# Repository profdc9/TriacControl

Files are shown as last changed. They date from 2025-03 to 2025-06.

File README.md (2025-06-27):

# TriacControl

This is an optoisolated triac motor speed controller where the phase control of the motor AC signal may be controlled by an analog or PWM signal.
Typically, a universal motor tool such as a drill or a router could have it's speed varied this way.
A PWM signal would usually be supplied by a microcontroller.  This motor speed control is open-loop and you have to add a tachometer
if you want to be able to vary the motor speed to achieve a particular rotation rate.

The voltage for the control may be 3.3 v, 5v, or up to 24 v.  A resistor (one of R17,R18,R19) and a capacitor (one of C2,C3,C4) determine how
the voltage/PWM signal varies the motor speed control.  The minimum control voltage to turn on the triac is about 1.75 V.  3.3V control uses
a 100 ohm resistor and a 22 uF capacitor, a 5 V control uses a 470 ohm resistor and a 47 uF capacitor, 12 volts uses a 2k2 resistor and 47 uF
capacitor, and 24 V uses a 4k7 resistor an 47 uF capacitor.  You may have to experiment to get it to put the control voltage into the required
range.  If you have an incandescent light bulb, you can use that as the load rather than the motor to see how bright it gets as you vary the
control voltage.  Three resistors and three capacitors may be placed on the board and selected using jumpers so that soldering need not be performed
to try different values.

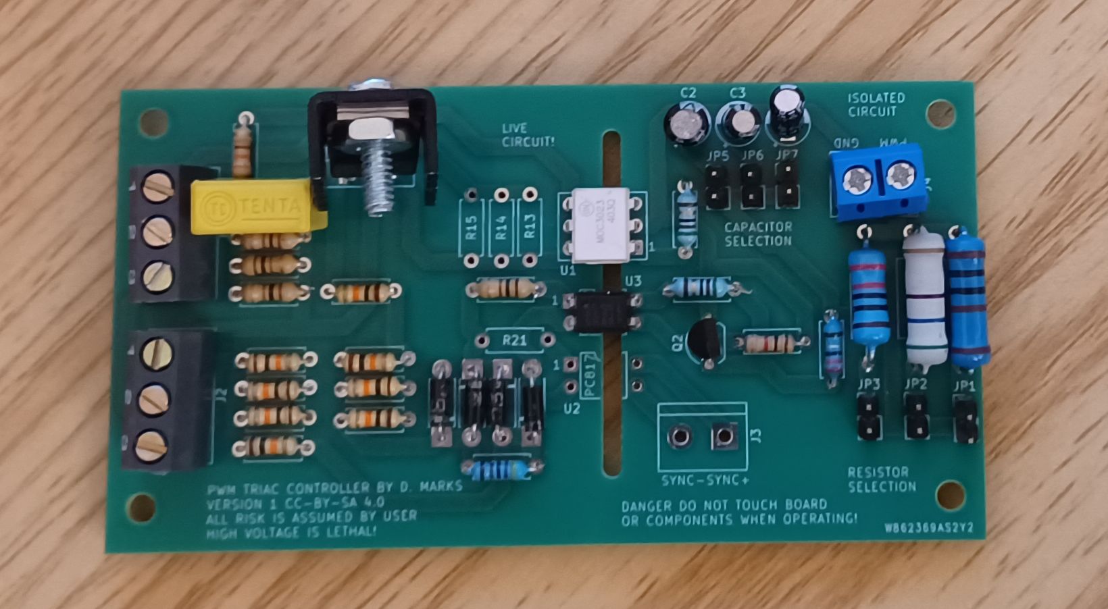
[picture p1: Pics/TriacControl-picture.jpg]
TriacControl


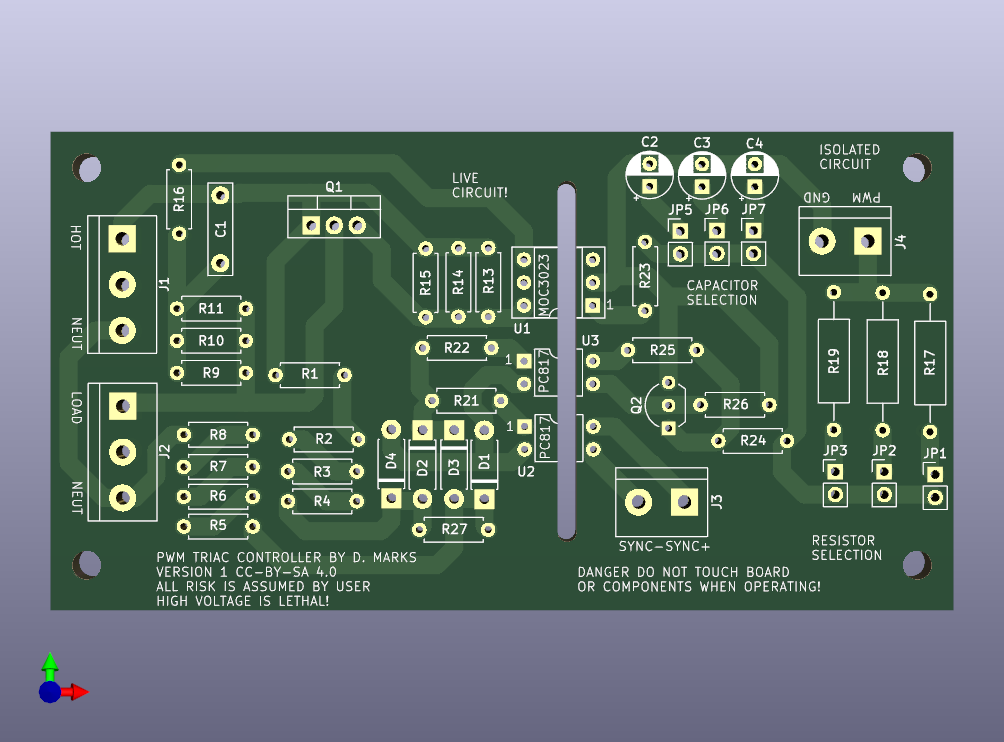
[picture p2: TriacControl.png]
TriacControl


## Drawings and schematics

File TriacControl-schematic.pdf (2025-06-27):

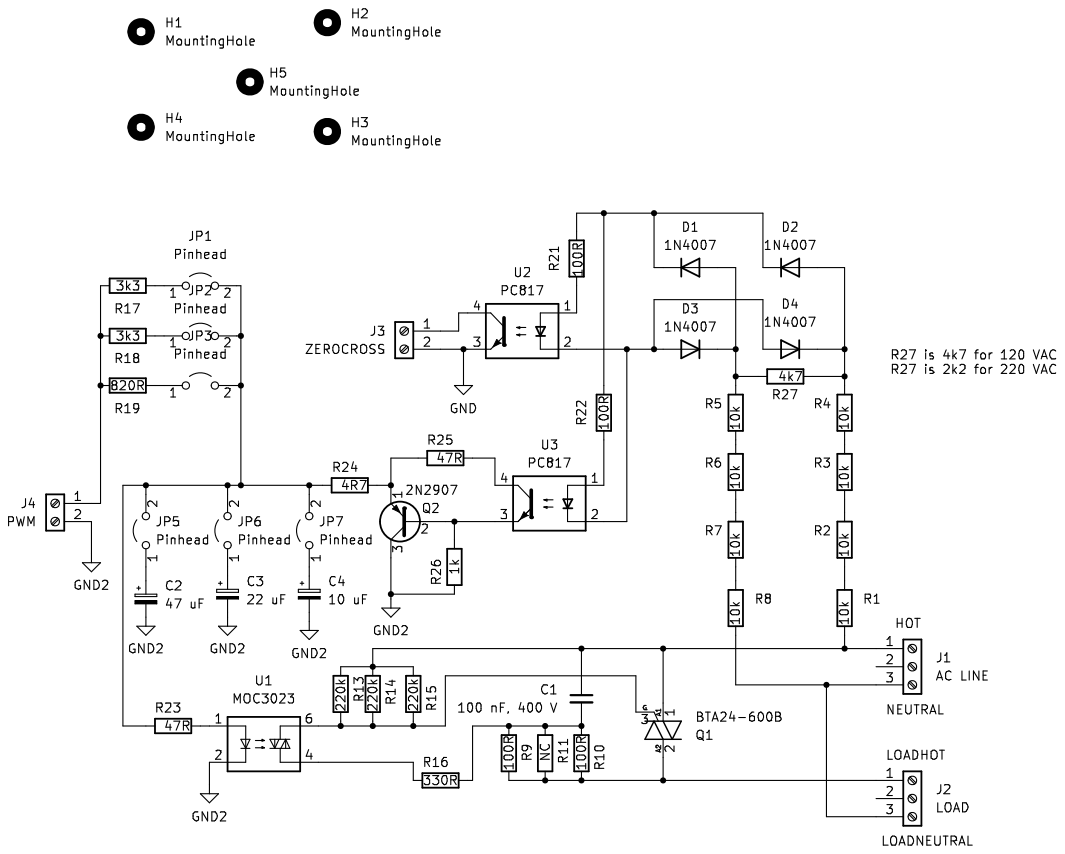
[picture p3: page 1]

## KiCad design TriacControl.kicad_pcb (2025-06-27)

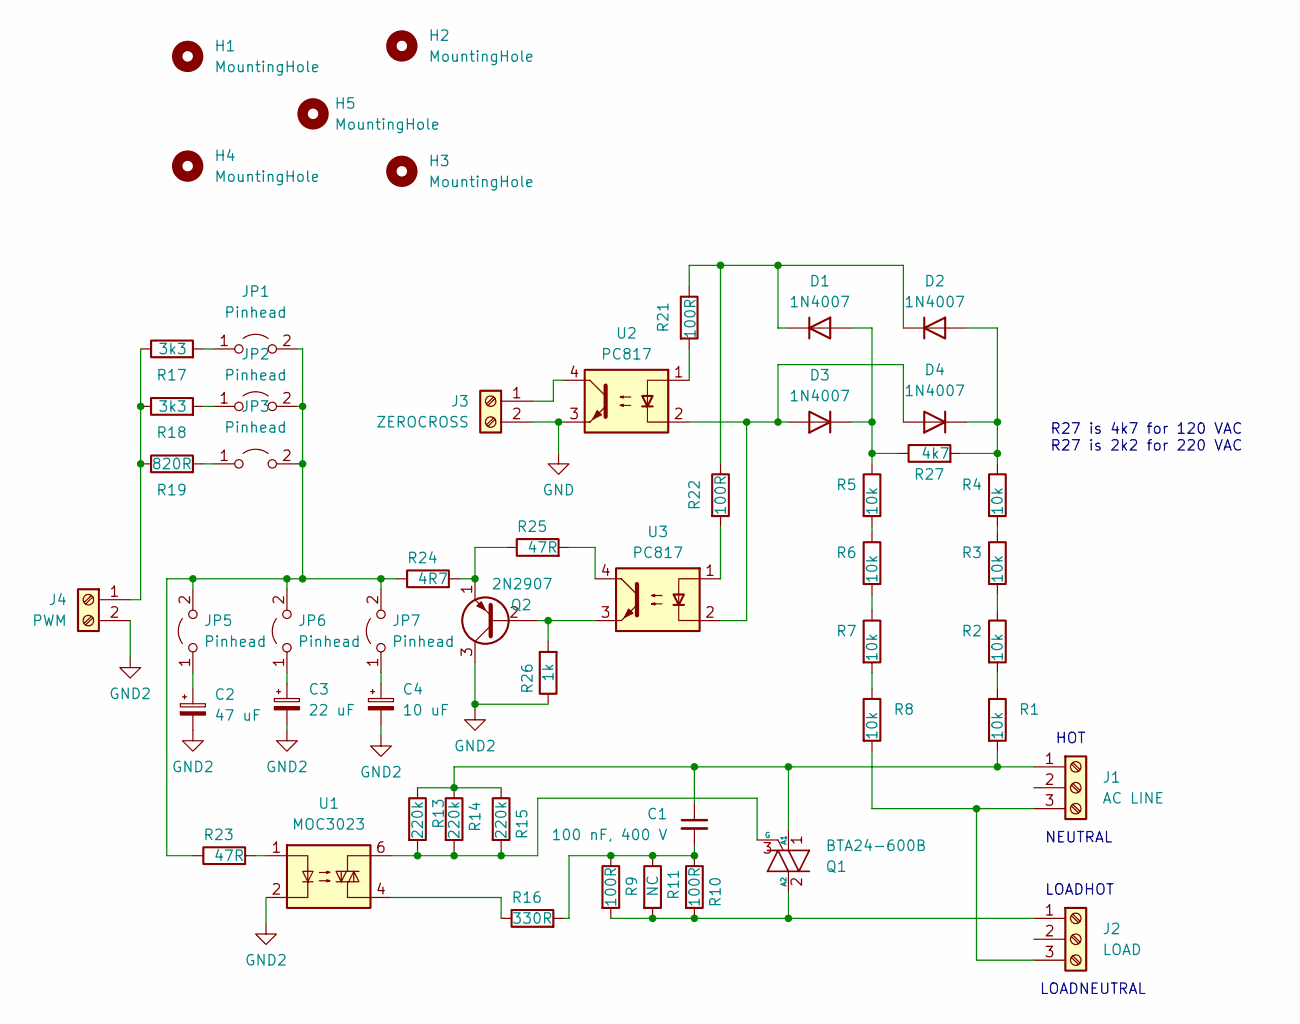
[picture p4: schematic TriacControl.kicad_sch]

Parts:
C1: 100 nF, 400 V; C_Rect_L10.0mm_W2.5mm_P7.50mm_MKS4
C2: 47 uF; CP_Radial_D5.0mm_P2.50mm
C3: 22 uF; CP_Radial_D5.0mm_P2.50mm
C4: 10 uF; CP_Radial_D5.0mm_P2.50mm
D1, D2, D3, D4: 1N4007; D_DO-41_SOD81_P7.62mm_Horizontal
H1, H2, H3, H4: MountingHole; MountingHole_3.2mm_M3
H5: MountingHole; MountingHole_2.1mm
J1: AC LINE; TerminalBlock_bornier-3_P5.08mm
J2: LOAD; TerminalBlock_bornier-3_P5.08mm
J3: ZEROCROSS; TerminalBlock_bornier-2_P5.08mm
J4: PWM; TerminalBlock_bornier-2_P5.08mm
JP1, JP2, JP3, JP5, JP6, JP7: Pinhead; PinHeader_1x02_P2.54mm_Vertical
Q1: BTA24-600B; TO-220-3_Vertical
Q2: 2N2907; TO-92_Inline_Wide
R1, R2, R3, R4, R5, R6, R7, R8: 10k; R_Axial_DIN0207_L6.3mm_D2.5mm_P7.62mm_Horizontal
R9, R10, R21, R22: 100R; R_Axial_DIN0207_L6.3mm_D2.5mm_P7.62mm_Horizontal
R11: NC; R_Axial_DIN0207_L6.3mm_D2.5mm_P7.62mm_Horizontal
R13, R14, R15: 220k; R_Axial_DIN0207_L6.3mm_D2.5mm_P7.62mm_Horizontal
R16: 330R; R_Axial_DIN0207_L6.3mm_D2.5mm_P7.62mm_Horizontal
R17, R18: 3k3; R_Axial_DIN0309_L9.0mm_D3.2mm_P15.24mm_Horizontal
R19: 820R; R_Axial_DIN0309_L9.0mm_D3.2mm_P15.24mm_Horizontal
R23, R25: 47R; R_Axial_DIN0207_L6.3mm_D2.5mm_P7.62mm_Horizontal
R24: 4R7; R_Axial_DIN0207_L6.3mm_D2.5mm_P7.62mm_Horizontal
R26: 1k; R_Axial_DIN0207_L6.3mm_D2.5mm_P7.62mm_Horizontal
R27: 4k7; R_Axial_DIN0207_L6.3mm_D2.5mm_P7.62mm_Horizontal
U1: MOC3023; DIP-6_W7.62mm_Socket
U2, U3: PC817; DIP-4_W7.62mm

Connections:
GND: J3.2, U2.3
GND2: C2.2, C3.2, C4.2, J4.2, Q2.3 (C), R26.1, U1.2
unnamed: C1.2, R9.1, R10.1, R11.1, R16.2
unnamed: D1.2 (A), D3.1 (K), R5.1, R27.1
unnamed: D1.1 (K), D2.1 (K), R21.1, R22.1
unnamed: D2.2 (A), D4.1 (K), R4.1, R27.2
unnamed: D3.2 (A), D4.2 (A), U2.2, U3.2
unnamed: C1.1, J1.1, Q1.1 (A1), R1.2, R13.1, R14.1, R15.1
unnamed: J1.3, J2.3, R8.2
unnamed: J2.1, Q1.2 (A2), R9.2, R10.2, R11.2
unnamed: J3.1, U2.4
unnamed: J4.1, R17.1, R18.1, R19.1
unnamed: JP1.1 (A), R17.2
unnamed: JP1.2 (B), JP2.2 (B), JP3.2 (B), JP5.2 (B), JP6.2 (B), JP7.2 (B), R23.1, R24.1
unnamed: JP2.1 (A), R18.2
unnamed: JP3.1 (A), R19.2
unnamed: C2.1, JP5.1 (A)
unnamed: C3.1, JP6.1 (A)
unnamed: C4.1, JP7.1 (A)
unnamed: Q1.3 (G), R13.2, R14.2, R15.2, U1.6
unnamed: Q2.2 (B), R26.2, U3.3
unnamed: Q2.1 (E), R24.2, R25.1
unnamed: R1.1, R2.2
unnamed: R2.1, R3.2
unnamed: R3.1, R4.2
unnamed: R5.2, R6.1
unnamed: R6.2, R7.1
unnamed: R7.2, R8.1
unnamed: R16.1, U1.4
unnamed: R21.2, U2.1
unnamed: R22.2, U3.1
unnamed: R23.2, U1.1
unnamed: R25.2, U3.4

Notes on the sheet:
LOADNEUTRAL
R27 is 4k7 for 120 VAC R27 is 2k2 for 220 VAC
NEUTRAL
LOADHOT
HOT

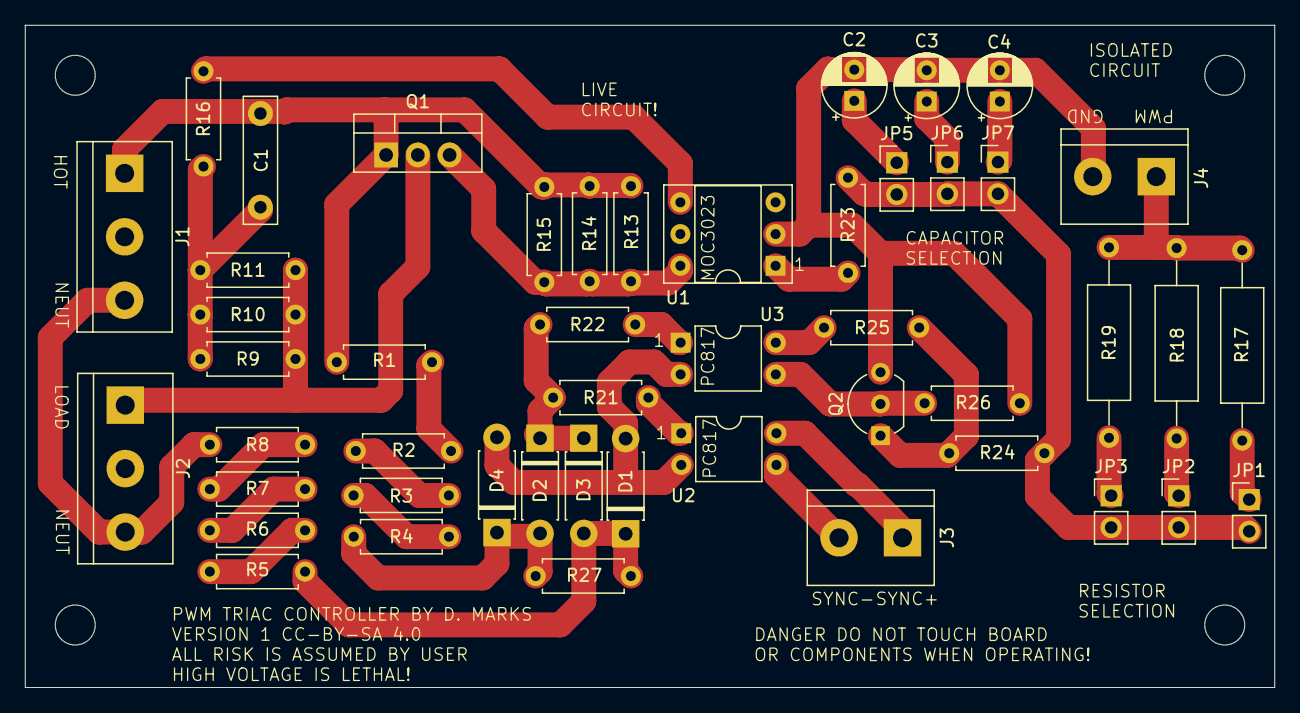
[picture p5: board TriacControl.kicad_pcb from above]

Board: 2 copper layers, 100.0 x 53.0 mm, 53 parts (0 on the bottom side), 33 nets.

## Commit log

2025-01-28 A few changes
    [Phase-PWM-Manipulation.sch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]
2025-01-29 Changed values, moved parts
    [TriacControl-B_Cu.gbr, TriacControl-B_Mask.gbr, TriacControl-B_Paste.gbr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]
2025-01-30 Fixed names and traces
    [TriacControl-B_Cu.gbr, TriacControl-B_Mask.gbr, TriacControl-B_Paste.gbr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]
2025-01-30 Changed connection to snubber, resistor size, etc.
    [TriacControl-B_Cu.gbr, TriacControl-B_Mask.gbr, TriacControl-B_Paste.gbr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]
2025-01-31 Fixed positioning of component
    [TriacControl-B_Cu.gbr, TriacControl-B_Mask.gbr, TriacControl-B_Paste.gbr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]
2025-03-11 Moved snubber capacitor
    [TriacControl-B_Cu.gbr, TriacControl-B_Mask.gbr, TriacControl-B_Paste.gbr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]
2025-03-26 Moved components a little ore
    [TriacControl-B_Cu.gbr, TriacControl-B_Mask.gbr, TriacControl-B_Paste.gbr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]
2025-06-12 Added snubber capacitor calculation
    [TriacControl.kicad_pcb, TriacControl.kicad_sch]
2025-06-27 Updated TRIAC and snubber circuit
    [TriacControl.kicad_pcb, TriacControl.kicad_sch]

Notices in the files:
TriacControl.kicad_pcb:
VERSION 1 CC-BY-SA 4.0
